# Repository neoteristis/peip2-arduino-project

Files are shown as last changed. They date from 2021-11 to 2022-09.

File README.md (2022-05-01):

# PolyDog V1

## Presentation

> This project has taken place during the Arduino Class of the second year of prep school at Polytech Nice Sophia.  
> In the text, "We" will represent Raphaël Anjou and Hugo Durand, who worked together on this project.  
> We had four months to build any project we wanted as long as it used Arduino hardware. A robot dog was an idea that we found very challenging and entertaining.

> Dozens of other robots inspired us to do this project and helped us in the design of our robot.

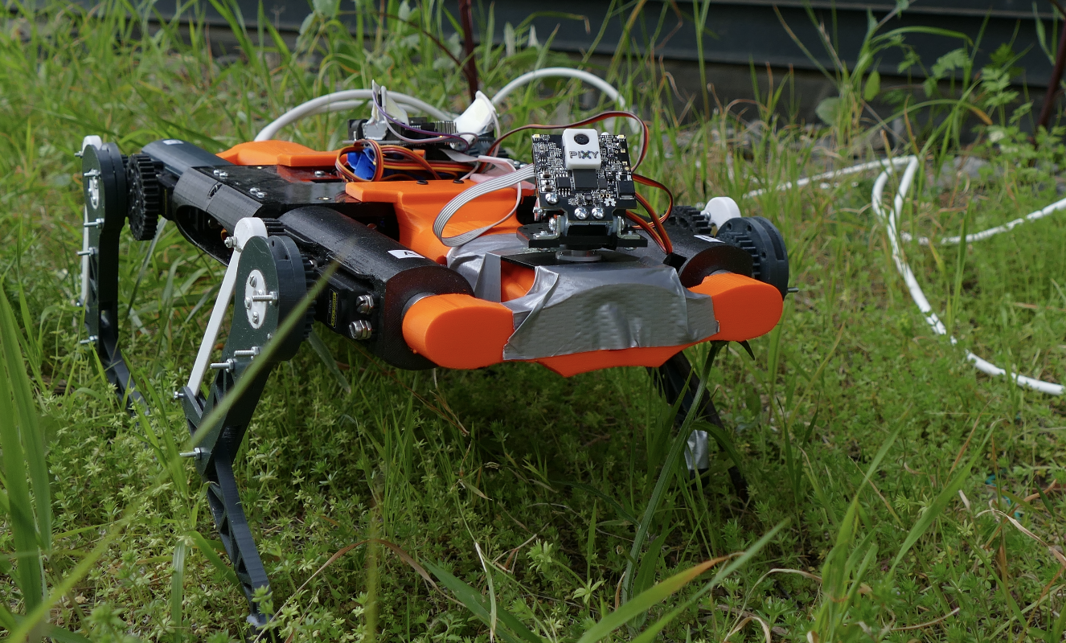
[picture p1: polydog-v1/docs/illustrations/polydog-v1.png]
Robot Pictures


## Summary

- [PolyDog V1](#polydog-v1)
  - [Presentation](#presentation)
  - [Summary](#summary)
  - [Robot Parts](#robot-parts)
    - [Leg parts](#leg-parts)
    - [Body parts](#body-parts)
    - [Electronic Components](#electronic-components)
  - [Flowchart](#flowchart)
    - [Initialization](#initialization)
    - [Remote Control](#remote-control)
    - [Camera](#camera)
    - [Movements](#movements)

## Robot Parts

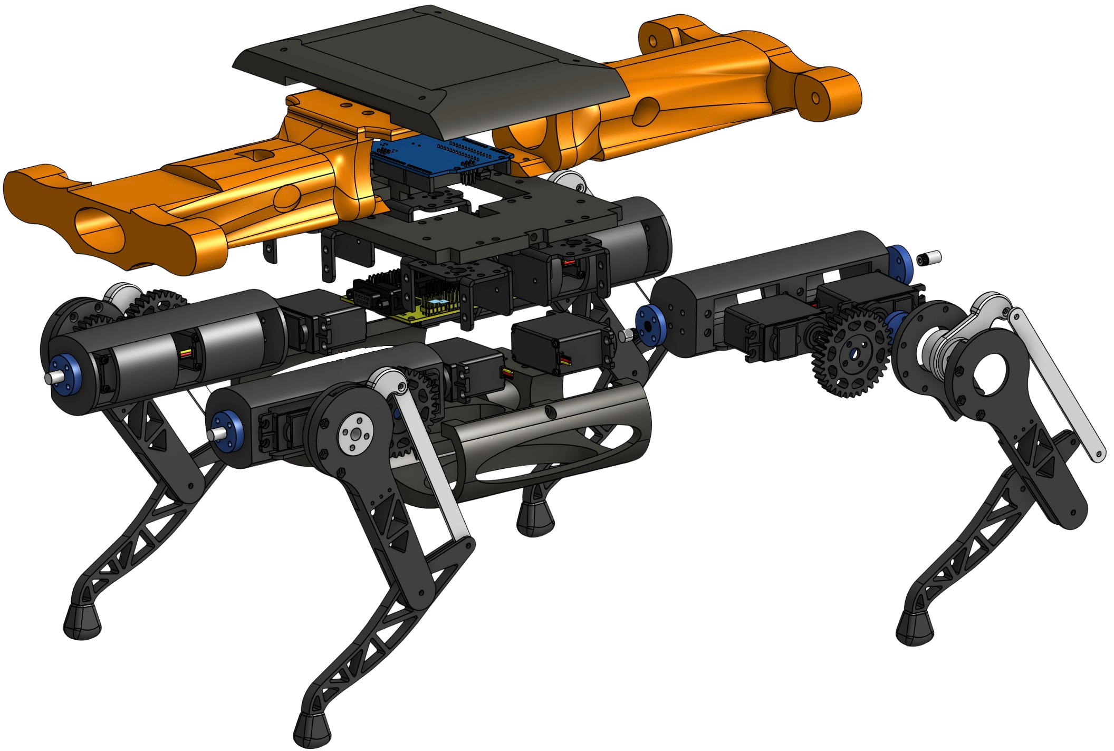
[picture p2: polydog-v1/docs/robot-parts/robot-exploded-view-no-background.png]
PolyDog exploded view


### Leg parts

<table> <!--Table-->
<tbody> <!--Table Body-->
    <tr> <!-- TABLE HEADER -->
        <th align="center" width="80">Name</th>
        <th align="center" width="250">Preview</th>
        <th align="center">Description</th>
        <th align="center" width="75">Material</th>
    </tr>
    <tr> <!--Line-->
        <td align="center">Femur</td>
        <td align="center">
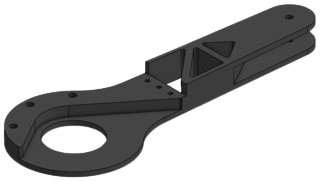
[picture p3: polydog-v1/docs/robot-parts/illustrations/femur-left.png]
            
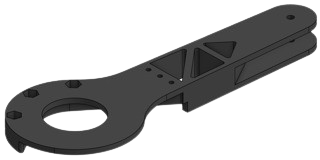
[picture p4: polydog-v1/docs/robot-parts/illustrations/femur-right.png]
            
        </td>
        <td align="center">Attached to the hip to hold the knee. Is connected to the tibia.</td>
        <td align="center">3D-printed</td>
    </tr>
    <tr> <!--Line-->
        <td align="center">Foot</td>
        <td align="center">
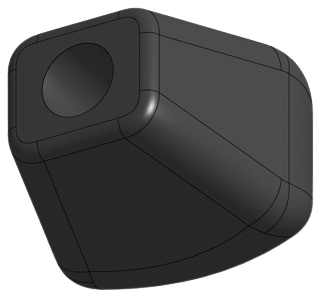
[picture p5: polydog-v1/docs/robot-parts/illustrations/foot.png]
            
        </td>
        <td align="center">Attached at the end of every tibia, it helps with the grip on the floor.</td>
        <td align="center">3D-printed</td>
    </tr>
    <tr> <!--Line-->
        <td align="center">Gear</td>
        <td align="center">
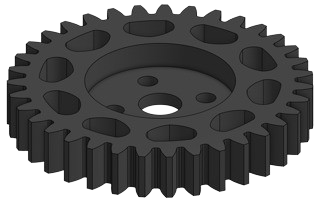
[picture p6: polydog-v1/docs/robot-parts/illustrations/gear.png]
            
        </td>
        <td align="center">Attached to the servo responsible for the whole leg movement. Is connected to the hip.</td>
        <td align="center">3D-printed</td>
    </tr>
    <tr> <!--Line-->
        <td align="center">Hip</td>
        <td align="center">
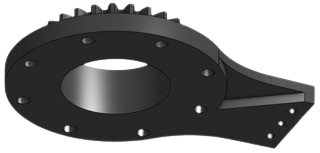
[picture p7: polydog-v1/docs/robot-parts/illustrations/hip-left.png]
            
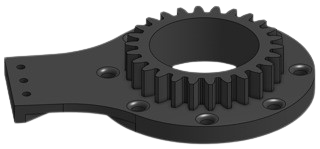
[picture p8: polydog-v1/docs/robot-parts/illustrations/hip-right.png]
            
        </td>
        <td align="center">Link between the servo motor for the whole leg and the femur. Is moved by a gear. Hold the knee in place.</td>
        <td align="center">3D-printed</td>
    </tr>
    <tr> <!--Line-->
        <td align="center">Knee</td>
        <td align="center">
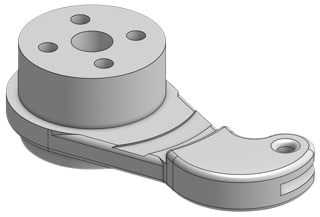
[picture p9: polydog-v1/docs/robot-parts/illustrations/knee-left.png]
            
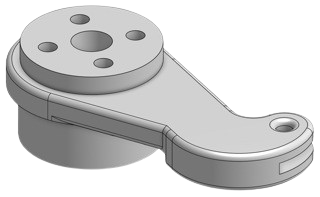
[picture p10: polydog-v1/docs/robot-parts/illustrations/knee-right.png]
            
        </td>
        <td align="center">Link between the servo motor for the knee and the tendon to make the anatomical knee move. Directly attached to the servo.</td>
        <td align="center">3D-printed</td>
    </tr>
        <tr> <!--Line-->
        <td align="center">Leg Holder</td>
        <td align="center">
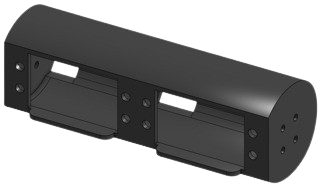
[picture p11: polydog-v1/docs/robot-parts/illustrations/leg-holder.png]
            
        </td>
        <td align="center">Hold the two servo motors necessary to make the leg move.</td>
        <td align="center">3D-printed</td>
    </tr>
    <tr> <!--Line-->
        <td align="center">Tendon</td>
        <td align="center">
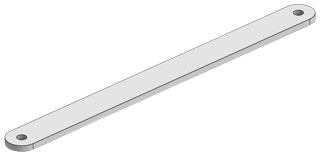
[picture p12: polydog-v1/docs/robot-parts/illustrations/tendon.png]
            
        </td>
        <td align="center">Link between the knee and the tibia.</td>
        <td align="center">3D-printed</td>
    </tr>
    <tr> <!--Line-->
        <td align="center">Tibia</td>
        <td align="center">
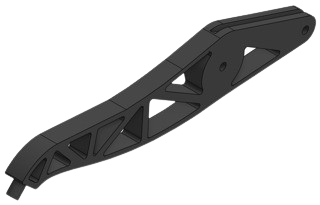
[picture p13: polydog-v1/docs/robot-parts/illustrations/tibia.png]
            
        </td>
        <td align="center">Link between the foot, the femur and the tibia. Is moved by the tendon and rotates around the point where the femur is attached.</td>
        <td align="center">3D-printed</td>
    </tr>
</tbody>
</table>

### Body parts

<table> <!--Table-->
<tbody> <!--Table Body-->
    <tr> <!-- TABLE HEADER -->
        <th align="center" width="95">Name</th>
        <th align="center">Preview</th>
        <th align="center">Description</th>
        <th aling="center" width="75">Material</th>
    </tr>
    <tr> <!--Line-->
        <td align="center">Back</td>
        <td align="center">
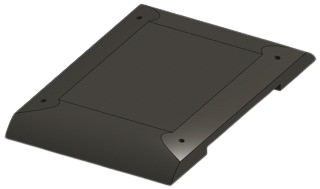
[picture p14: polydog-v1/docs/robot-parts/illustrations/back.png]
            
        </td>
        <td align="center">Close the robot body to protect and hide all the hardware and cables inside.</td>
        <td align="center">3D-printed</td>
    </tr>
    <tr> <!--Line-->
        <td align="center">Base</td>
        <td align="center">
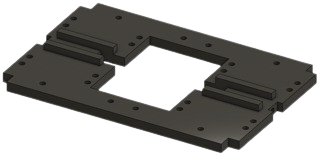
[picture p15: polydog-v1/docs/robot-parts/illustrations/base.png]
            
        </td>
        <td align="center">Core of the body structure.</td>
        <td align="center">3D-printed</td>
    </tr>
    <tr> <!--Line-->
        <td align="center">Ribs</td>
        <td align="center">
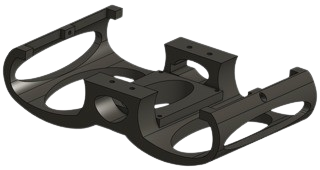
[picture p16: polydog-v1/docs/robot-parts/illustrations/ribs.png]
            
        </td>
        <td align="center">Help with the rigidity of the whole body. Protect the hardware from being hit. Hold the SSC-32.</td>
        <td align="center">3D-printed</td>
    </tr>
    <tr> <!--Line-->
        <td align="center">Servo Bracket</td>
        <td align="center">
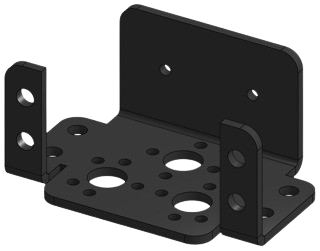
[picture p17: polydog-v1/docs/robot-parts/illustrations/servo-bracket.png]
            
        </td>
        <td align="center">Hold one servo motor in place.</td>
        <td align="center">Aluminium</td>
    </tr>
    <tr> <!--Line-->
        <td align="center">Spine</td>
        <td align="center">
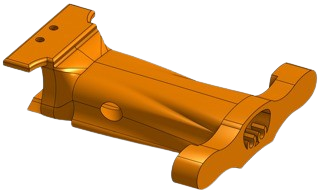
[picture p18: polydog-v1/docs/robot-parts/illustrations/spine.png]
            
        </td>
        <td align="center">Hold two legs and store the power cable.</td>
        <td align="center">3D-printed</td>
    </tr>
</table>
</tbody>

### Electronic Components

<table> <!--Table-->
<tbody> <!--Table Body-->
    <tr> <!-- TABLE HEADER -->
        <th align="center" width="95">Name</th>
        <th align="center">Preview</th>
        <th align="center">Description</th>
    </tr>
    <tr> <!--Line-->
        <td align="center">Arduino UNO</td>
        <td align="center">
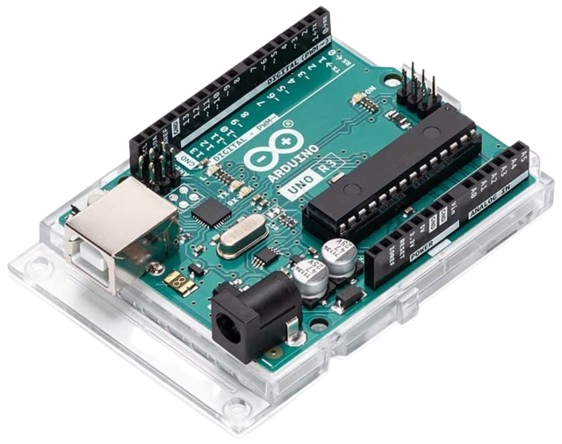
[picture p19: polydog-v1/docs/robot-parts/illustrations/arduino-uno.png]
            
        </td>
        <td align="center">Robot brain.</td>
    </tr>
    <tr> <!--Line-->
        <td align="center">SSC-32 Servo Controller</td>
        <td align="center">
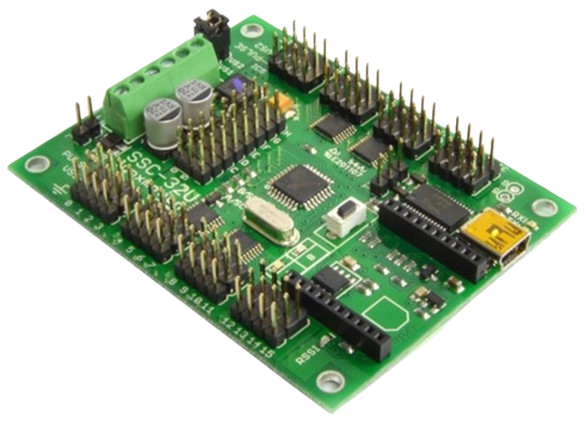
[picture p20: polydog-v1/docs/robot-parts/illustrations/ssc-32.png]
            
        </td>
        <td align="center">Receives command from the Arduino UNO to control every servo motor.</td>
    </tr>
    <tr> <!--Line-->
        <td align="center">Servo motors</td>
        <td align="center">
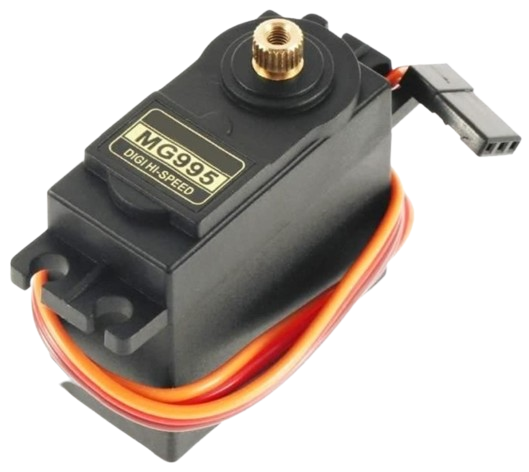
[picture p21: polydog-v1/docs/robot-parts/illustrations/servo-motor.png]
            
        </td>
        <td align="center">Moves the part of the body they are connected to.</td>
    </tr>
    <tr> <!--Line-->
        <td align="center">Infrared Remote & Receiver</td>
        <td align="center">
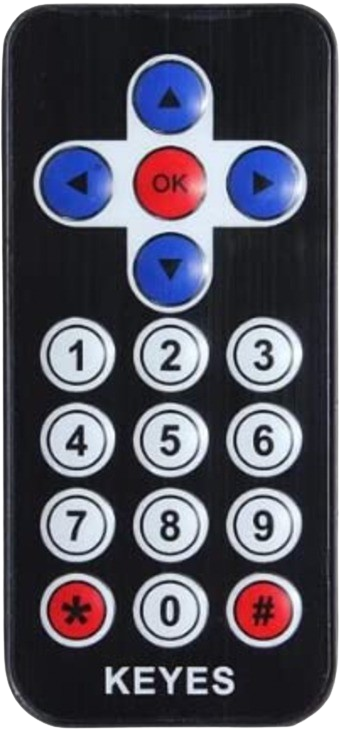
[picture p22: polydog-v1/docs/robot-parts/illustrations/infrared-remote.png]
            
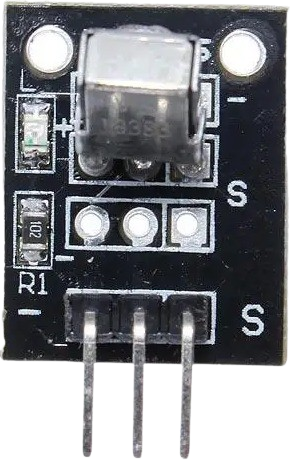
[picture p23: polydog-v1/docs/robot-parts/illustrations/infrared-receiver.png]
            
        </td>
        <td align="center">Remote control of the robot movements and actions.</td>
    </tr>
    <tr> <!--Line-->
        <td align="center">Pixy Cam 2 & Mount</td>
        <td align="center">
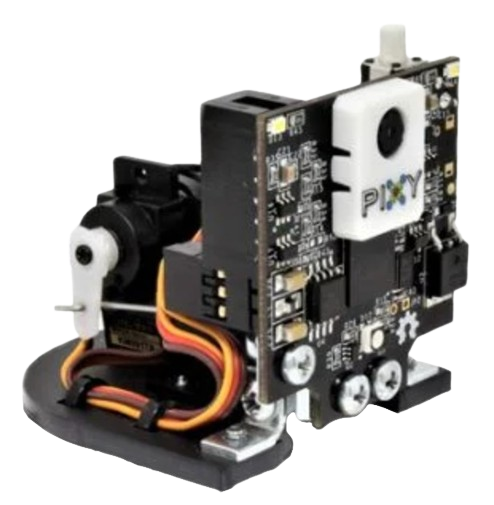
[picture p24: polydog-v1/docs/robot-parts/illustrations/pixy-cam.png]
            
        </td>
        <td align="center">Camera of the robot. Is able to detect colors. The camera can be moved on 2 axis with it's mount.</td>
    </tr>
    <tr> <!--Line-->
        <td align="center">Power source</td>
        <td align="center">
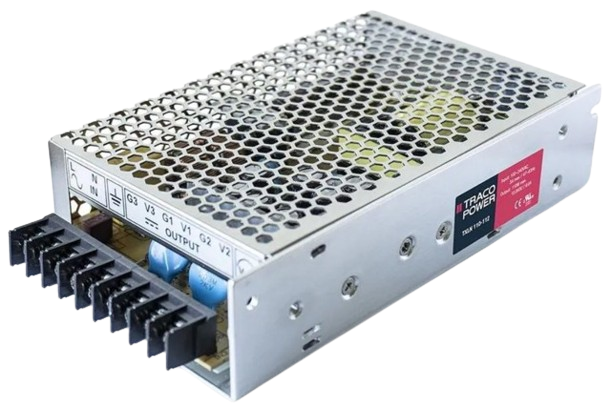
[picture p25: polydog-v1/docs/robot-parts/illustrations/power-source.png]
            
        </td>
        <td align="center">Powers all the electronic components. 30 Amperes and 5 Volts. </td>
    </tr>
</table>
</tbody>

## Flowchart

### Initialization

### Remote Control

### Camera

### Movements

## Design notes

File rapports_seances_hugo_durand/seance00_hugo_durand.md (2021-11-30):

# Première séance : 

début novembre jusqu'au 02/12/2021 

## Emergence de l'idée

Pendant les vacances, je me suis beaucoup documenté sur la plupart des projets Arduino les plus connus. Au début j'étais sûr d'une chose, je voulais créer un robot capable de se déplacer. Raphael était du même avis. 

J'ai alors été intérressé par la cartographie d'une pièce par une voiture, le serpent, l'araignée, la self-balancing robot. En retombant par hasard, sur une vidéo du célébre robot Spot de Boston Dynamics, nous n'avons pas hésité longtemps. On fera un robot chien qui naitra sous le nom de PolyDog.

## Recherche sur les prototypes à notre portée

Au fur et à mesure que l'on cherche, on trouve de plus en plus d'exemples de prototypes. Je me suis d'abord penché sur la patte de notre robot, de comment elle pourrait fonctionner.

Deux manière de faire observée :

- Loki le Dev, un développeur spécialisé en système embarqué et robotique opte pour 3 actionneurs basé sur un système de parallélogramme.

- KiTty bot lui possède un servo moteur directement sur le genou et je trouve ça moins optimisé, du fait que la patte est plus lourde et l'inertie de la patte est augmentée.

On a opté pour la 1ere option. Je l'ai contacté sur Discord pour qu'il m'aiguille sur quelques points et avoir son avis sur notre projet. Il a été très sympa et nous a beaucoup aidés dans le début de nos recherches.

Enfin, on a appris que le défi, une fois le robot construit, sera de le faire tenir debout en équilibre sur ces pattes à l'aide d'un algorithme complexe basé sur le reverse kinematics. On devra entraîner la demarche du robot sur unity, afin qu'il se déplace convenablement.

## Création et impression des pièces

Nous allons créer pour commencer une jambe miniature de notre robot pour manipuler son fonctionnement.

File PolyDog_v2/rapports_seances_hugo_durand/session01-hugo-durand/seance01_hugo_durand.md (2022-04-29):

# Séance 1 - version 2 de PolyDog

## Semaine du 04 avril 2022 - 17 avril 2022

-----

Nous avons eu des difficultés à se mettre en route pour commencer la deuxième version de notre robot chien : PolyDog_v2.

**1. Étape 1 - Bilan et synthèse de la v1 -**

Les points noirs de la version 1 sont :

* Le poids trop élevé du corps. Masse volumique du PETG trop grande.

* Les servo-moteurs ont un couple trop faible (13kg/cm). Le robot a du mal à effectuer des mouvements (cumulé avec un poids trop important)

* L'engrenage entre la hanche et le servo-moteur. L'embout en plastique s'use facilement. Le degré de liberté d'un pas de pignon augmente.

##### Corps en aluminium

Nous avons donc décidé de réaliser le corps du robot en aluminium, assemblé avec des équerres et des charnières.

<figure align="center">
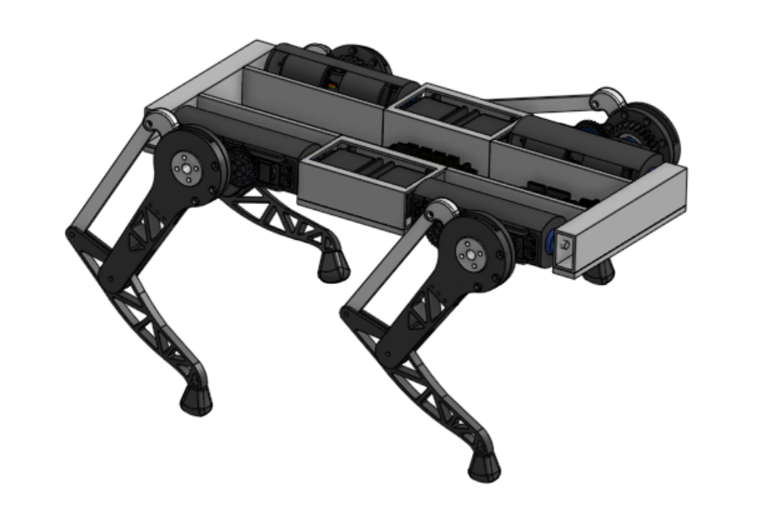
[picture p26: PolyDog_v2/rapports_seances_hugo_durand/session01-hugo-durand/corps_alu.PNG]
  
  <figcaption>Des carrés d'alu viennent se fixer sur une plaque en aluminium ou de plexiglass</figcaption>
</figure>

##### Engrenage double hélice

Pour renforcer la stabilité de l'engrenage, j'ai modélisé deux double helical gear qui vont se coincer dans la roue dentée double helice de la hanche. J'ai trouvé cette idée sur YouTube : https://www.youtube.com/watch?v=pxgut7d135w&t=162s

Cela donne ceci :

<figure align="center">
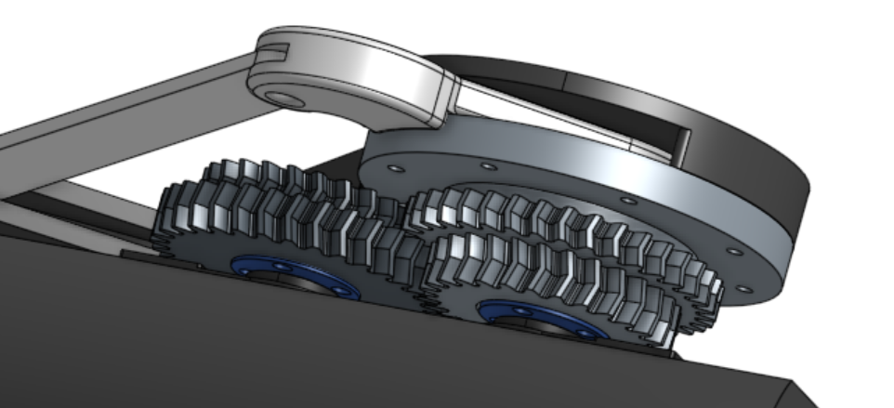
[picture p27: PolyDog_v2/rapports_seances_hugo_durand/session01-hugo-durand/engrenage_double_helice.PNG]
  
  <figcaption></figcaption>
</figure>

>Je n'ai pas encore réussit à modifier l'angle d'offset pour que les deux roues dentées soit synchronisé deux à deux.

En attendant j'ai prédéfini le matériel à acheter pour la construction du corps en aluminium.

**Achat matos:**

* carre d'alu : 32mm (longueur), 16mm (largeur_intérieur), 28 (hauteur_intérieur) ---> prévu 4mm d'épaisseur
<br>
* carre d'alu : 200mm (longeur), 58mm (largeur_intérieur) 28 (hauteur_intérieur) --->prévu 4mm d'épaisseur, je n'y connais rien
<br>
* plaque d'alu ou plaque de pléxiglass: 5mm d'épaisseur, 414 x 184mm;

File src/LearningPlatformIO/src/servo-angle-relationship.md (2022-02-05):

# Servo Angle Relationship

## Context

We are considering the following names for the legs :

> B --- A -> B-A is the front \
> | ....... | \
> | ....... | \
> | ....... | \
> C --- D -> C-D is the rear

Considering X the name of the leg, all motors will be named with the following convention :

- X_hip
- X_knee
- X_shoulder

## Placement of all the motors on the robot

1. A_shoulder
2. A_hip
3. A_knee
4. B_knee
5. B_hip
6. B_shoulder
7. C_shoulder
8. C_hip
9. C_shoulder
10. D_knee
11. D_hip
12. D_shoulder

> 4 --- 3 -> Front \
> 5 ..... 2 \
> 6 ..... 1 \
> 7 ..... 12 \
> 8 ..... 11 \
> 9 --- 10 -> Rear

## Angle relationship

As a baseline, we will use the angles of the A leg. \
Which means that all others should be expressed in function of A_motor_angle.

1. A_shoulder_angle -> baseline
2. A_hip_angle -> baseline
3. A_knee_angle -> baseline
4. B_knee_angle ->
5. B_hip_angle ->
6. B_shoulder_angle -> ?
7. C_shoulder_angle -> ?
8. C_hip_angle -> map(0, 180, 180, 0)
9. C_shoulder_angle -> map(0, 180, 180, 0)
10. D_knee_angle -> baseline
11. D_hip_angle -> baseline
12. D_shoulder_angle -> ?

## TODO

Change A leg motor placement

## TO NOTE BETTER

Pour le genou : 90 degrés
Pour la hanche : 180 degrés

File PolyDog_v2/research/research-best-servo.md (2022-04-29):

| Servo name | Couple | Weight| Rotation speed | Price | Reference |
| :---: | :---: | :---: | :---: | :---: | :---: |
|TowerPro Metal Gear MG995 (**Polydog_v1**)| Couple de décrochage : 13 kg/cm (4,8 V)|55 g | 0,17 sec/60 ° | / | https://www.youtube.com/channel/UCp-MOXWuPocJWpOKq-EK11g |
|Servomoteur HS-85MG Hitec | 3.5 Kg-cm | 21.9g | Vitesse (sec/60o): 0.13 | 33,20 € | https://www.robotshop.com/eu/fr/servo-moteur-hs85mg-hitec.html |
|Servo numérique étanche DS3225MG|maximum torque can reach 21kg.cm (5,0 V)| 67g|(5,0 V): 0,15 sec / 60 degrés|23,99€|https://www.amazon.fr/dp/B08BZNSLQF?tag=takoe-21&linkCode=osi&th=1&psc=1&keywords=Servomoteurs|
|Servo TD-8135MG|35.7 km cm (5,0 V)| 85g|(5,0 V): Noload speed:0.32sec/60°-0.22sec/60° / 60 degrés|$17.99 |https://www.ebay.com/itm/283885400511|
|Coreless digital servo TD-8135MG (**Polydog_v2**)|Couple de décrochage de pointe: 32.7kg.cm - 35.2kg.cm| 56g|Vitesse à vide: 0.32sec/60 ° - 0.22sec/60 °|13,90 euros |https://fr.aliexpress.com/item/4000538643378.html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|

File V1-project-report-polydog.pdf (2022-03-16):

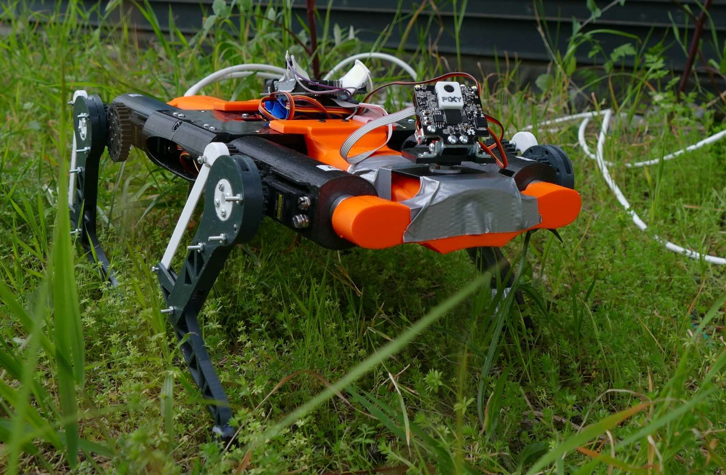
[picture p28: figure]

– Polytech Nice-Sophia – | 2021-2022
ANJOU Raphaël | Peip2 – Arduino
DURAND Hugo | M. Pascal MASSON

# RAPPORT DE PROJET ROBOT POLYDOG

Fig. 1 : Le PolyDog dans son habitat naturel

2

## SOMMAIRE

Planification / Réalisation

Hardware

Software

3

## Introduction

Dans le cadre du cours d’Électronique-Arduino de la 2ème année du cycle préparatoire à l’école de Polytech Nice Sophia, nous avons eu l’occasion de créer de A à Z un projet de notre choix. Le temps imparti pour cette réalisation était de 8 séances de TD étalées sur un peu plus de 3 mois. Cependant, nous avons commencé à réfléchir à ce que l’on avait le plus envie de construire un mois avant le début des cours.

Le but de ce projet était de nous donner le goût d’innover grâce à des technologies que nous n’utilisions pas telles que la découpe laser, l’impression 3D ou le fer à souder. Il avait pour vocation de nous former au travail en équipe, ainsi que nous permettre de mettre un pied dans le métier d’ingénieur. Pour ce faire, le projet a débuté par la présentation d’un cahier des charges, d’un diagramme de Gantt. Le suivi du projet a ensuite eu lieu grâce à la rédaction de rapports de séance incluant tout le travail fournit entre deux séances.

En effectuant nos recherches sur Internet, principalement YouTube, nous avons pu trouver de nombreux exemples de ce qui était faisable grâce à l’Arduino. Nous étions sûr de deux choses, nous voulions que ce soit un robot qui puisse se déplacer et que ce soit une première dans l’école. Nous avons hésité entre un bras robotisé automatisé ou un robot issu du biomimétisme.

C’est à ce moment que jaillit l’idée d’un robot chien que nous avons baptisé POLYDOG. Nous l’avons conçu dans le but de déplacer un corps à 4 pattes dans les 4 directions basique : gauche, droite, avant, arrière. Il est doté d’une PixyCam et d’un module Infrarouge pour une communication à distance des mouvements.

Ainsi, la problématique de notre sujet est : Par quels moyens déplacer un robot sur 4 pattes ?

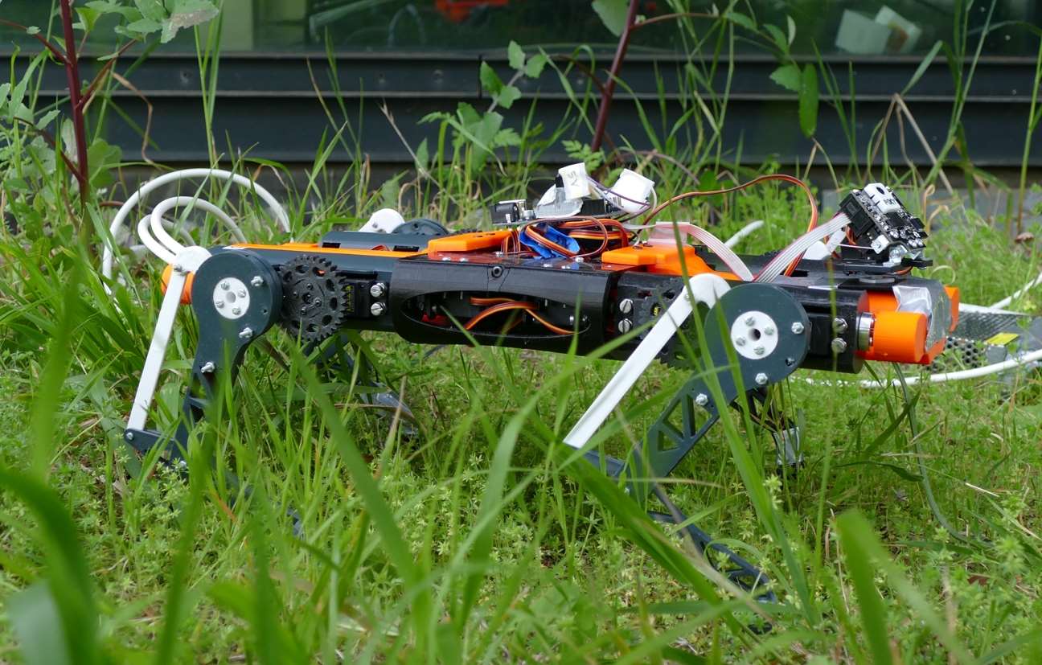
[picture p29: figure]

Fig. 2 : Le PolyDog se cache dans les fourrés

4

## Cahier des charges

### Reprenons notre cahier des charges initial et faisons un point sur les objectifs que nous nous étions fixés :

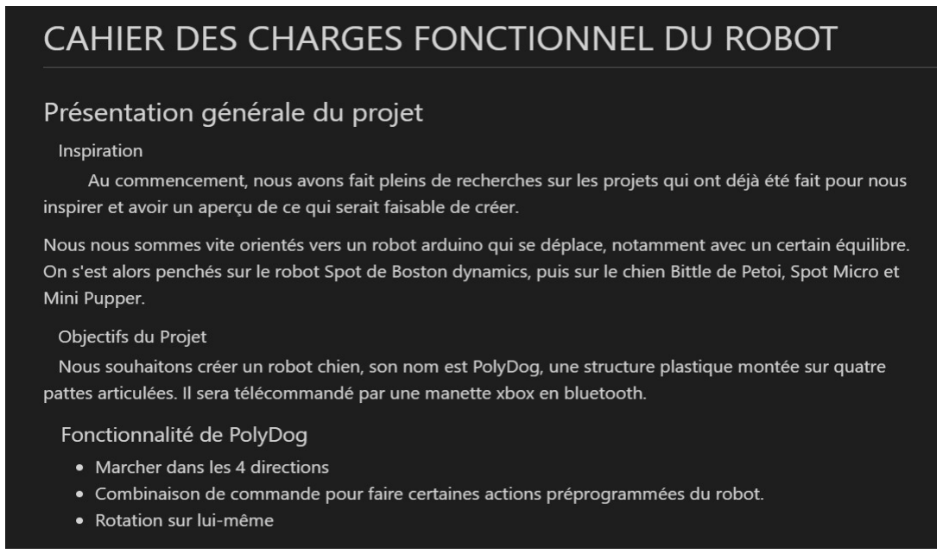
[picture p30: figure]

### 2.1/ Fonctionnalités réalisées

Nous avons quasiment rempli l’objectif principal : notre robot peut marcher en avant et sur les côtés, avec des combinaisons de commande pour faire certaines actions préprogrammées du robot.

Cependant, nous avions pour objectif qu’il soit télécommandé par une manette de Xbox. Nous ne sommes pas arrivés à ce degré de complexité, en revanche, nous avons équipé le robot de commandes à distance infrarouges.

De plus, nous n’avons pas eu la possibilité de réaliser la fonctionnalité lui permettant de tourner sur lui-même.

### 2.2/ Fonctionnalités optionnelles

Nous avons équipé Polydog, d’une caméra intelligente qui suit un objet d’une certaine couleur. Le module PixyCam installée sur son socle à l’avant du robot. Lorsqu’elle détecte un objet bleu, le robot avance tout droit.

5

### 2.3/ Diagramme de Gantt et Planning réel

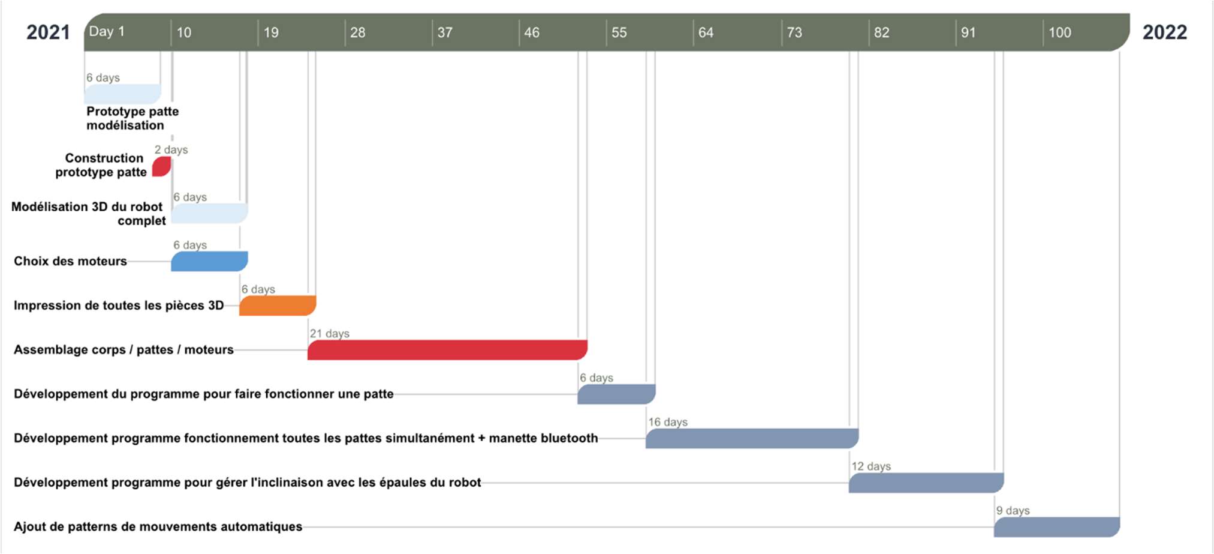
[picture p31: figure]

Fig. 3 : Diagramme de Gantt initial

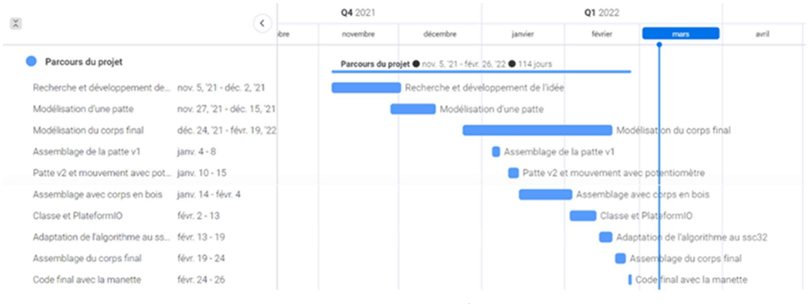
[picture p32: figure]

Fig. 4 : Planning réel

La modélisation 3D du robot complet a pris beaucoup plus de temps que prévu. Cela vient du fait de l’évolution de notre vision du robot et de ses composants. Il faut savoir que nous avons eu beaucoup de problème au niveau de la puissance des moteurs et de l’équilibre du robot. Pensant que le problème venait de la gestion des circuits de la carte, nous avons changé 4 fois de système électronique :

- Driver Adafruit + ArduinoNano
- ArduinoMega2560+ Base Shield + SensorShield (Empilés les uns sur les autres pour obtenir les pins adéquat)
- MegaStrong + Board micro controller intégré
- ssc32- servo controller + Arduino UNO

A chaque changement de système, nous avions l’impression de revenir en arrière du fait de devoir changer le programme et aussi l’organisation des pattes pour des raisons parfois inconnues.

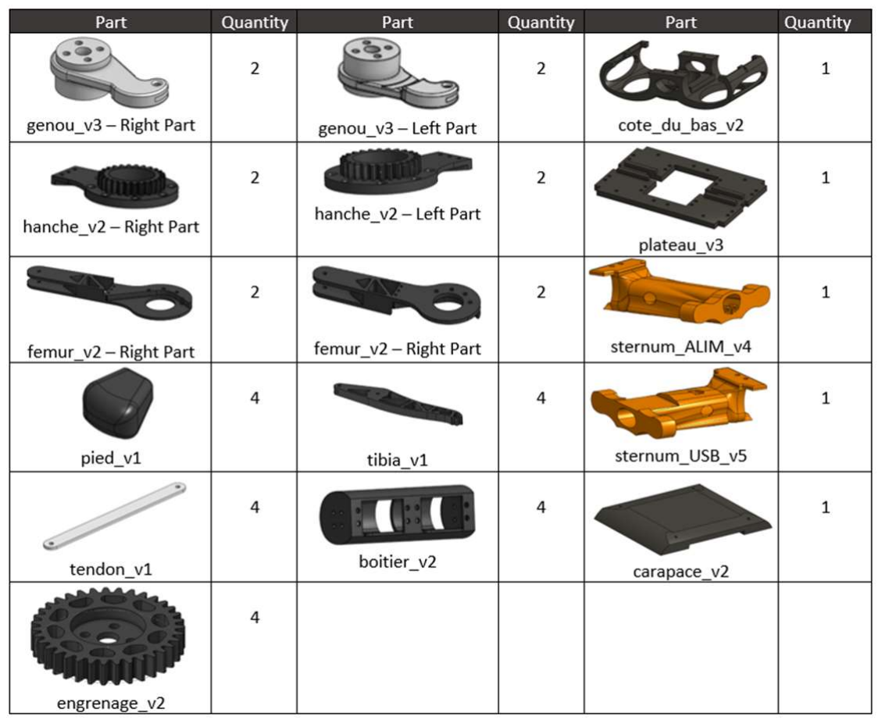
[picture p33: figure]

6

# Hardware

### 3.3/ Pièce 3D

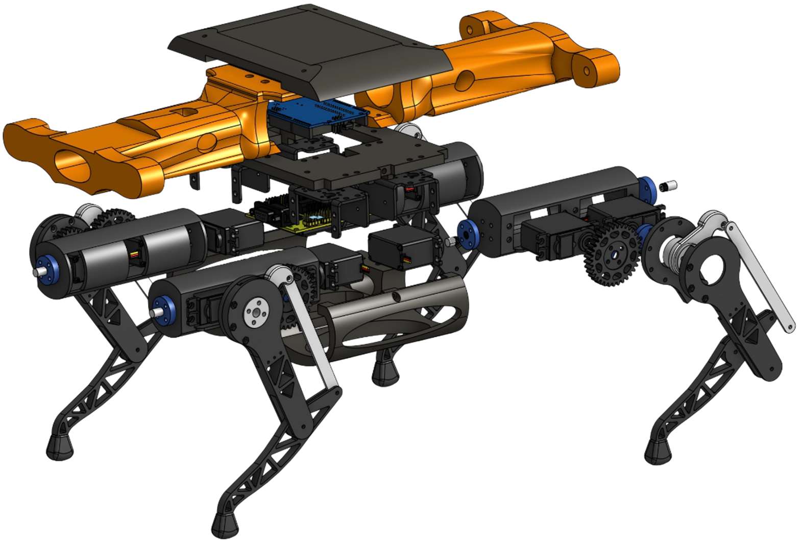
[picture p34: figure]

La conception a été réalisé sur OnShape, un logiciel en ligne, gratuit pour les étudiants.
Le boîtier pour les moteurs a été choisi circulaire pour pivoter avec plus de liberté de gauche à droite.

Nous avons rencontré des difficultés dans la conception de certaines pièces. Les côtes du bas devait s’emboiter avec le plateau avec les moteurs déjà fixés dessus. Nous avons dû faire face également au problème du poids. Les deux pièces sternum et les côtes du bas ont été optimisées pour peser le moins possible tout en gardant une certaine solidité.

Durant l’assemblage, 2 pièces ont été endommagées. Avec un peu de colle, l’emboîtement a pu se faire sans trop de
problèmes.

Cependant, le montage du robot entier en abandonnant le
corps en bois l’a rendu trop lourd ce qui a réduit ses capacités de mouvement.

Le poids cumulé de toutes les pièces pèse sur l’équilibre et la mobilité des pattes.

Cependant, nous ne regrettons pas, car nous y avons appris beaucoup de choses : conserver une marge entre les pièces car l’impression a une imprécision de 0,4 mm ; mettre des inserts dans le plastique ; choisir minutieusement l’emplacement des vis.

Si c’était à refaire, j’opterais pour un corps encore plus léger, en dépits que les fils pendraient sur le côté et au-dessus du robot. Le rendu final serait moins ordonné mais plus mobile.

Composition du robot :

Il mesure 17,6 cm de large sur 42,4 cm de long. Il pèse environ 2 kilogrammes.

### 37 pièces 3D indépendantes

assemblées avec 142 vis,
plus de 142 écrous et 14
inserts.

Le temps d’impression peut s’estimer à plus de 100
heures.

7

### 3.2/ Fonctionnement de la patte

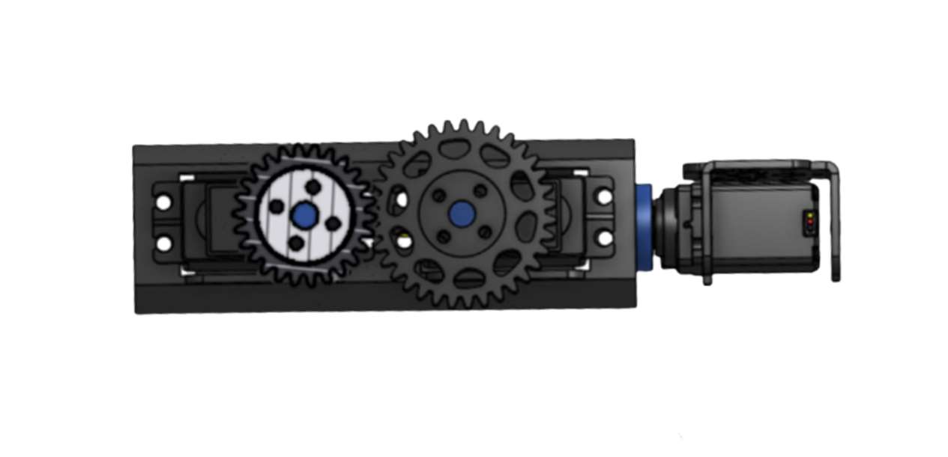
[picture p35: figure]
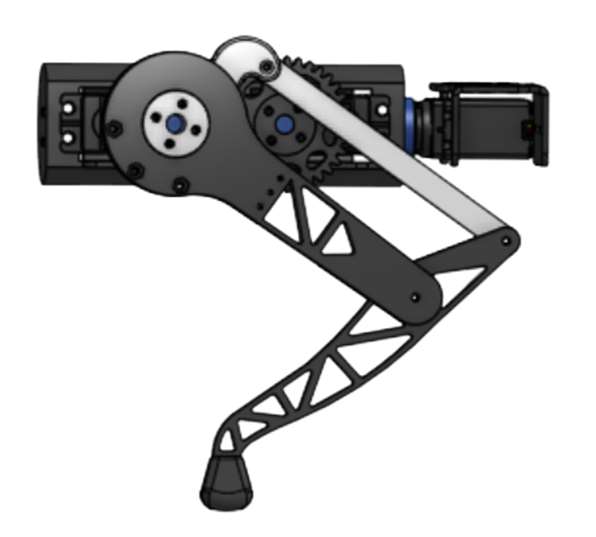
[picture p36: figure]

Nous avons opté pour un fonctionnement d’une patte avec le modèle du parallélogramme. Les moteurs sont centralisés au niveau du corps du robot pour garder la patte légère et une optimisation du mouvement.

Une patte du robot est munie de 3 servos moteurs. Le 1er servo en partant de la gauche est celui qui bouge le genou (au centre de la patte). Le genou est positionné de tel sorte que l’amplitude de mouvement (0° à 180°) du servo associé correspondent aux angles désirés.
Le 2e
est relié à un engrenage de 35 dents vers 26 dents qui bouge la hanche. De ce fait le rapport entre les deux engrenages augmente l’amplitude de mouvement de la hanche de 1,35, pour obtenir 0° minimal jusqu’à 242° maximal.
Le 3e
est fixé au corps principal du robot et permet de faire pivoter la patte sur le côté. Pour soutenir le boitier, on place une fixation pivot à l’autre extrémité.

Le pied du robot est fait en plastique élastique caoutchouteux. Cela permet d’obtenir une plus grande adhérence au sol.

### 3.3/ Composants électroniques

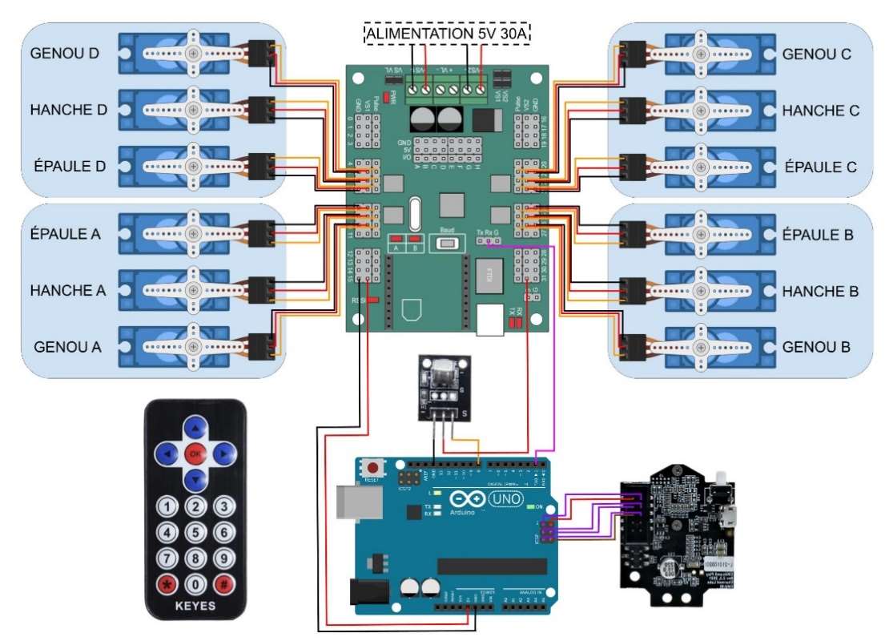
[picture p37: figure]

Nous avons ici, l’ensemble des composants électroniques utilisés pour notre projet. Nous avons 12 servo moteurs branchés sur un ssc32-servo controller qui communique par l’intermédiaire du Serial avec une Arduino UNO. Cette dernière est le composant central puisqu’elle relie sur ses ports, la PixyCam et le récepteur infrarouge. L’ensemble est alimenté sur secteur par l’intermédiaire d’une alimentation de 5V et 30A.

8

# Software

### 4.1/ Classes du programme

La partie code de notre projet a été implantée sur un espace de travail PlateformIO. Il permet de créer un code source unique pour de multiples environnements facilement (Arduino Uno, Mega 2560, etc). Dans le dossier source, nous avons 3 classes :

- CustomServos :

Cette classe permet de communiquer avec le SSC32 en indiquant seulement un angle. On instancie un objet de cette classe à partir d’un numéro de pin.

void CustomServo::move(int position, int time) | Par l’intermédiaire de la carte Arduino, on envoie des
{ | commandes sur le Serial du ssc-32. Le message
Serial.print("#"); | envoyé est de la forme « #{numéro_pin} P {position
Serial.print(_pin); | entre 500 et 2500} T {time}
Serial.print(" P");
Serial.print(position); | Nous n’utilisons pas le paramètre temps dans la
Serial.print(" T"); | fonction move. Cela nous permet d’avoir la liberté de
Serial.println(time); | faire varier le temps dans les méthodes codant les
} | mouvements du robot.
void CustomServo::write(int angle) | La fonction write renvoie la fonction move en
{ | convertissant l’amplitude 500-2500° en 0-180°. Cela
move(map(angle, 0, 180, 500, 2500), 0); | facilite la compréhension physique des mouvements
}
- Leg :

Permet de contrôler chaque moteur d’une jambe sans se soucier des décalages. Par exemple, les moteurs de la hanche n’ont pas les mêmes orientations entre la gauche et la droite. Pour permettre une synchronisation des moteurs des 4 pattes, nous avons pour certains, ajouter un offset de 170°.

- PolyDog :

Cette classe est en quelque sorte un répertoire des méthodes qui vont permettre de donner vie à notre chien. On y définit la méthode self_balancing(), hold_shoulder(), move_forward(), move_right(), move_left(), etc

Les angles de chacun des servos moteurs sont choisis à partir de nombreux test d’optimisation du mouvement de la patte.

void PolyDog::hold_shoulders() | Voici un exemple simple d’une méthode dans la classe Polydog.
{ | Cette méthode maintient les pattes perpendiculaires au sol.
legA.move_shoulder(90);
legB.move_shoulder(90); | On remarque que cette méthode utilise la classe Leg pour gérer les
legC.move_shoulder(90); | décalages dû à notre installation des servo moteurs.
legD.move_shoulder(90);

du robot.

9

### 4.2/ Algorigramme

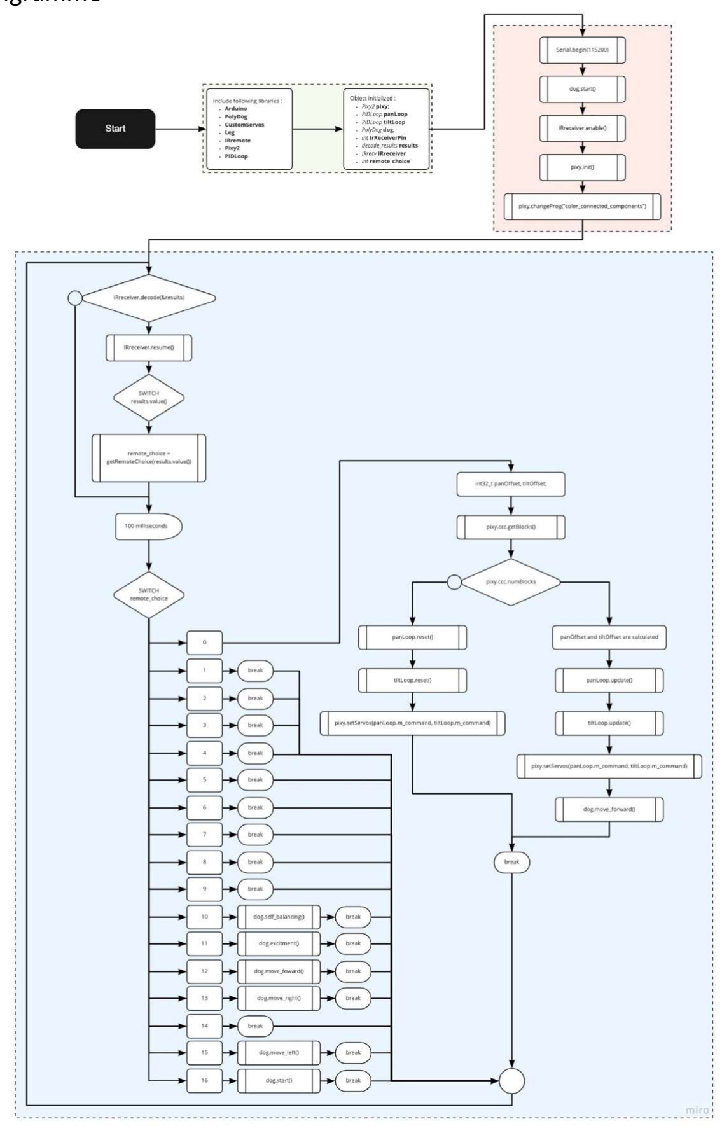
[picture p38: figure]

Les librairies et modules sont d’abord importés (partie verte). Ensuite, les objets utilisés sont instanciés au début du programme (partie rouge). C’est à ce moment-là que le robot est allumé ainsi que la PixyCam et la communication infrarouge. Le robot est alors debout. Enfin, une boucle détectant l’appui des boutons de la télécommande permet de choisir les actions du robot. Par exemple, si l’on appuie sur le bouton 0, le robot utilise la PixyCam pour détecter s’il y a un objet bleu. Si c’est le cas, il se dirige vers l’avant, sinon il se maintient debout. Les autres boutons lui permettent d’effectuer un enchainement de mouvement en boucle ou de se déplacer.

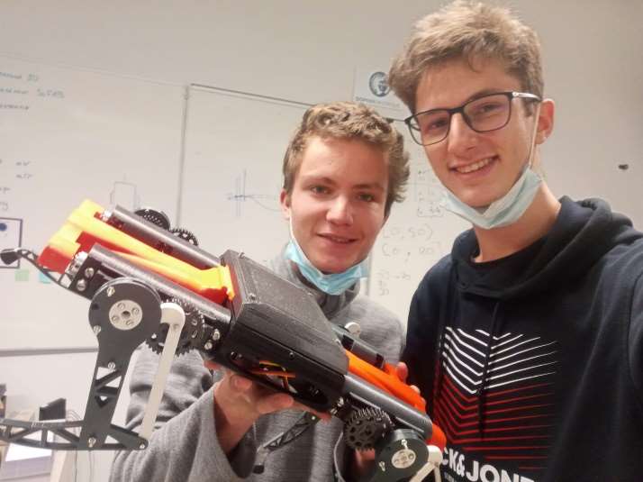
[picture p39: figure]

10

# Conclusion

Ce projet Arduino était motivant et nous a apporté beaucoup de nouvelles compétences. Nous avons appris que le temps de réalisation d’une tâche est très variable. Nous nous sommes formés sur l’utilisation de nouveau outils et de nouveaux logiciels. Notre perception du projet a évolué au fur et à mesure de notre gain d’expérience.

C’est une belle aventure qui nous a fait découvrir le monde de la robotique. Cela a conforté Hugo dans son choix d’aller en robotique l’année prochaine et a conforté Raphaël dans son choix d’aller en SI.

# Perspective

Certes, notre robot chien Polydog marche et est télécommandé. Nous avons pu placer une caméra intelligente qui n’était pas prévu au départ. Nous avons appris de beaucoup de nos erreurs et surmonter des difficultés telles que la non-réponse des servo-moteurs, des angles incohérents, des problèmes de communication entre cartes Arduino, etc…

Cependant, le résultat n’est pas réellement convaincant. Il avance et se déplace en général d’une distance très faible (1cm par seconde en moyenne). Pour certains mouvements, il faut le soutenir un petit peu pour l’alléger artificiellement.

C’est pourquoi, nous considérons ce robot, comme la version 1, le premier jet. Nous prévoyons de commencer une nouvelle version avec un corps en aluminium ou impression résine et de meilleurs servo moteurs, et surtout l’expérience acquise au cours de 3 mois de travail. Nous avons une dizaine de semaine pour le finir et nous sommes plus motivés que jamais pour y arriver.

## Bibliographie

Inspiration :

https://www.youtube.com/watch?v=3_MtMmjEwa4&t=180s

https://www.yeggi.com/q/boston+dynamics/

https://grabcad.com/library/walking-quadruped-robot-diy-1

Lien guide Lynxmotion ssc32-servo controller :

http://www.lynxmotion.com/images/data/lynxmotion_ssc-32u_usb_user_guide.pdf

Guide de mise en marche de la télécommande IR :

https://www.gotronic.fr/pj2-36228-2302.pdf

https://www.gotronic.fr/pj2-codes-gt017-2234.pdf

Notre chaîne YouTube :

https://www.youtube.com/channel/UCp-MOXWuPocJWpOKq-EK11g/featured

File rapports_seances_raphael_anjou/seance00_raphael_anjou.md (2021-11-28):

# Séance 0 : 23/11/2021 --> 01/12/2021

&nbsp;&nbsp;&nbsp;&nbsp;Le travail compris dans la séance 0 correspond au travail préliminaire effectué avec la première
séance en classe avec les enseignants.

### Étape 1 : Choix du projet

&nbsp;&nbsp;&nbsp;&nbsp;Hugo et moi-même souhaitions réaliser un robot capable de se déplacer et pouvant être téléguidé.
Très impressionné par le robot chien **Spot** de ***Boston Dynamics***, nous avons tout d'abord recherché si d'autres 
personnes avaient eu la même idée que nous et avaient réalisé des versions réduites de ce robot. 
Bien évidemment, des dizaines de projets similaires existent sur Internet. Cela nous a rassuré dans notre idée et nous a
motivé à avancer. C'était décidé, nous allions faire un robot chien !

### Étape 2 : Création et mise en place du github

&nbsp;&nbsp;&nbsp;&nbsp;Avant d'aller plus loin dans nos recherches, nous avons décidé de mettre en place au plus vite 
un repository github fonctionnel afin de pouvoir se partager facilement nos recherches. Nous utilisons aussi un groupe
discord dédié au projet Arduino.

La structure actuelle est la suivante : 

```
.
+-- docs
|   +-- cahier_des_charges.md
|   +-- liste_du_materiel.md
|   +-- masson_presentation_deroulement_projet.pdf
|   +-- masson_propositions_projets.pdf
|   +-- masson_tuto_github.pdf
+-- miniature_robot_parts
+-- rapports_seances_hugo_durand
+-- rapports_seances_raphael_anjou
+-- research
+-- robot_parts
+-- src
+-- test
+-- .gitattributes
+-- .gitignore
+-- CMakeLists.txt
+-- README.md
```

### Étape 3 : Création d'une milestone dans github ainsi que plusieurs issues
&nbsp;&nbsp;&nbsp;&nbsp;Nous avons créé une milestone dans github intitulée `Documents, research and setup of the project`.
Dans cette milestone, 10 issues ont été créées afin de lister les tâches nécessaires à faire avant même la première séance
de cours.

### Étape 4 : Recherches générales sur le projet

&nbsp;&nbsp;&nbsp;&nbsp;Cette étape nous a permis de se faire une idée globale des difficultés et challenges techniques
que nous allions rencontrer. Nous avons ainsi étudié le design de nombreux robots disponibles en ligne que ce soit au
niveau du fonctionnement, du design ou des matériaux utilisés.

&nbsp;&nbsp;&nbsp;&nbsp;Parmi nos investigations, Hugo a trouvé la chaîne Youtube de ***Loki Le Dev***. Celui-ci est en
train de réaliser un projet similaire au nôtre, mais dans des envergures bien plus grandes. Hugo l'a contacté et Loki a
été très cordial durant nos échanges et nous a même donné accès aux fichiers 3D d'une jambe de son robot.

&nbsp;&nbsp;&nbsp;&nbsp;Nous avons aussi fait des recherches techniques notamment sur les différents mécanismes permettant
de faire bouger une jambe. Il semble judicieux d'après ce que nous avons trouvé d'utiliser la technologie du "parallélogramme"
qui permet de garder les moteurs au niveau du corps du robot. Contrairement à d'autres méthodes qui nécessitent d'avoir
un moteur au niveau du genou, mais cela nous paraissait trop complexe.

&nbsp;&nbsp;&nbsp;&nbsp;Les recherches sur les algorithmes ont aussi commencés. Ainsi, nous allons probablement travailler
sur un programme capable de faire du "inverse dynamics" car celui-ci est plus simple et efficace que le "forward dynamics".
Nous avons aussi trouvé des exemples de simulations de robot permettant d'entraîner virtuellement notre robot à se déplacer
sur différents terrains.

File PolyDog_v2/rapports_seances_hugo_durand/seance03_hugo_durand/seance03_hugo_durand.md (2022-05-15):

# Séance 3 - version 2 de PolyDog

## Semaine du 09 mai

-----

Le processus d'impression est toujours un peu long. Il nous a fallu 1jours et 7heures pour imprimer les boîtiers. 21 heures pour une patte du robot. 

Nous avons été forcé de lancer deux fois les impressions de la patte parce que la première fois nous avons oublié de mettre des supports.

Enlever des supports nous prends à chaque fois beaucoup de temps. Deux des boîtiers de moteurs se sont fêlés en enlevant le support à l'interieur. Raphael a remis du plastique sur la fissure pour consolider le tout pour le moment. Si cela pète, on reimprimera de nouveau, en remodelisant le boîtier pour qu'il soit un peu plus solide.

En mettant les boîtiers dans leur emplacement, je me suis rendu compte que la longueur que j'avais calculer pour que cela rentre était erronée. Nous avons donc dû reculer l'emplacement des servos et scier une partie de la tranche du carré d'alu.

Concernant les engrenages, j'avais dans les séances précédentes créer un système d'engrenage avec deux pignons à chevrons superposés en contact avec deux autres pigons de cette façon : 

<figure align="center">
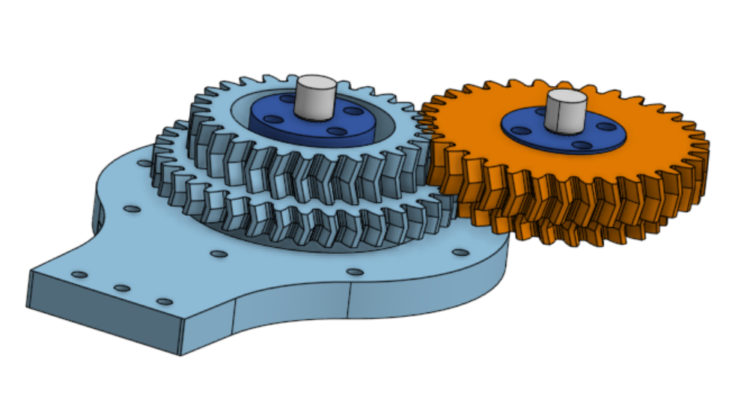
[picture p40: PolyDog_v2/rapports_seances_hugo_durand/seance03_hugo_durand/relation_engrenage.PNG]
  
  <figcaption></figcaption>
</figure>

Une fois imprimé, nous nous sommes rendu compte que les deux engrenages ne sont pas synchro, il y a un petit bloquage. Cependant indépendamment l'un de l'autre, les relations sont correcte. 

Ceci est peut être dû à Onshape qui ne conservent pas le clocking angle que je lui octroie. Donc la solution serait de le refaire sur Fusion360. Deuxième solution est de faire les pigons avec le même rapport de taille, et que les dents du petit pignons soit alignés avec celle du grand.

Si ceci ne fonctionne pas alors je garderai juste un des pignons de chaque.

Les maintiens de roulement ont tous été imprimés : 

<figure align="center">
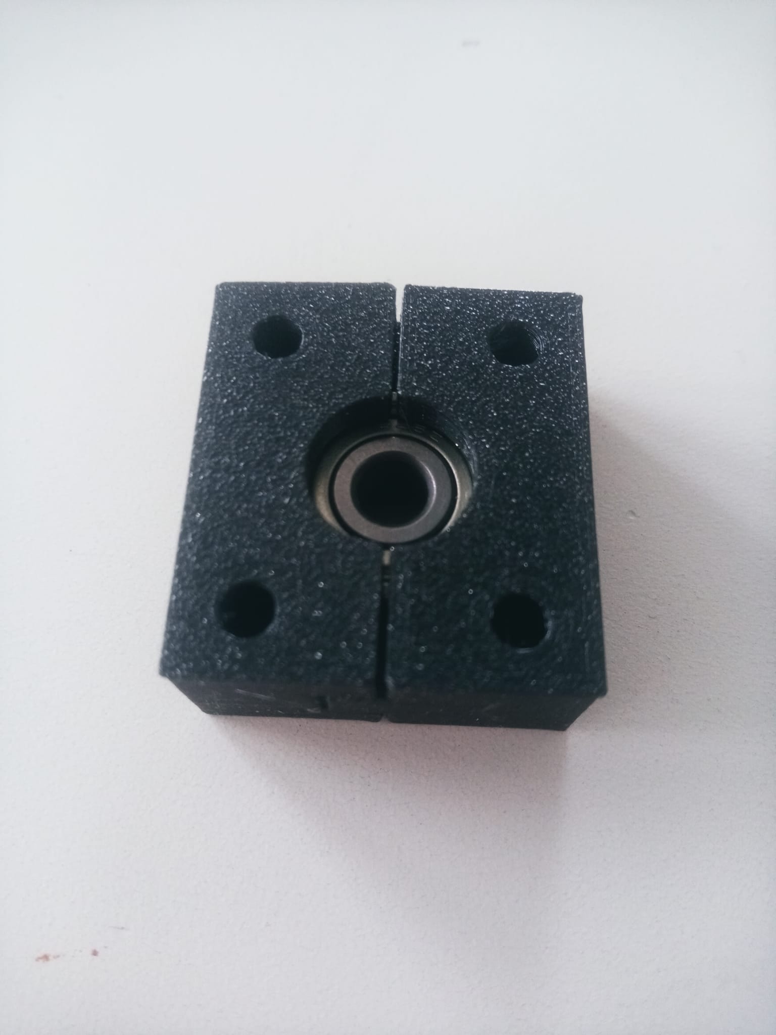
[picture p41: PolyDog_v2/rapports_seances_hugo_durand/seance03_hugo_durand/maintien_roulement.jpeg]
  
  <figcaption></figcaption>
</figure>

J'ai scié la tige en métal, fixer les embouts qui maintiennent le boîtier de la patte dans son axe.

J'ai compris ce qui n'allait pas dans les engrenages. Lorsque je faisais une vue ne coupe pour vérifier la relation entre les engrenages, je la faisais au milieu d'une tranche hélicoïdal. Je referais une nouvelle impression pour tester.

J'ai également renforcer les boîtiers de servo moteurs pour si jamais on les reimprime.

<figure align="center">
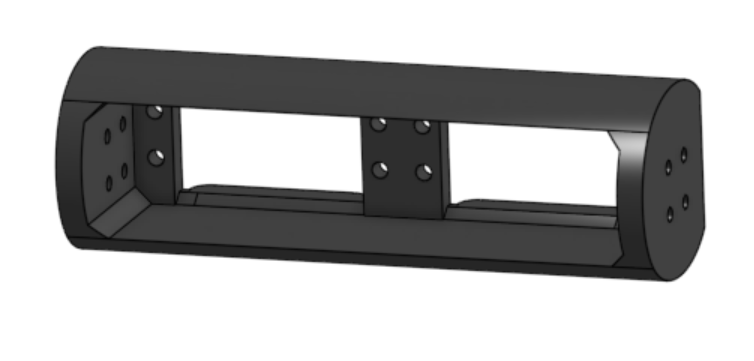
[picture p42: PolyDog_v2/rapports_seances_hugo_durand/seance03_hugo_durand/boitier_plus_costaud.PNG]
  
  <figcaption></figcaption>
</figure>

Pour finir j'ai crée les support de la carte ARDUINO UNO et le servo controller SSC32 :

<figure align="center">
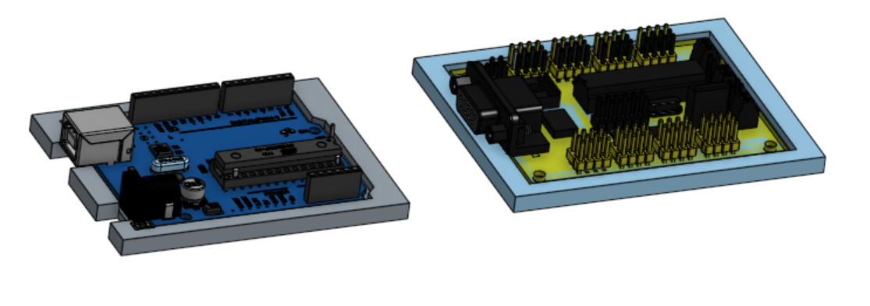
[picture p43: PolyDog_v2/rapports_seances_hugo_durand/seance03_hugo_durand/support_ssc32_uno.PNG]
  
  <figcaption></figcaption>
</figure>

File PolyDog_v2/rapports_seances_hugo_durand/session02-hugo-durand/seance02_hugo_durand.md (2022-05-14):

# Séance 2 - version 2 de PolyDog

## Semaine du 25 avril

-----

A castorama ou a leroy merlin, il n'y pas un éventail de taille et dimension extraordinaire. Nous avons donc constitué nos propres carrés d'alu.

On a chipé deux-trois plaques d'alu de différentes épaisseurs qu'on pouvait trouver.

On a commencer par la plaque d'alu, support principale du corps:

<figure align="center">
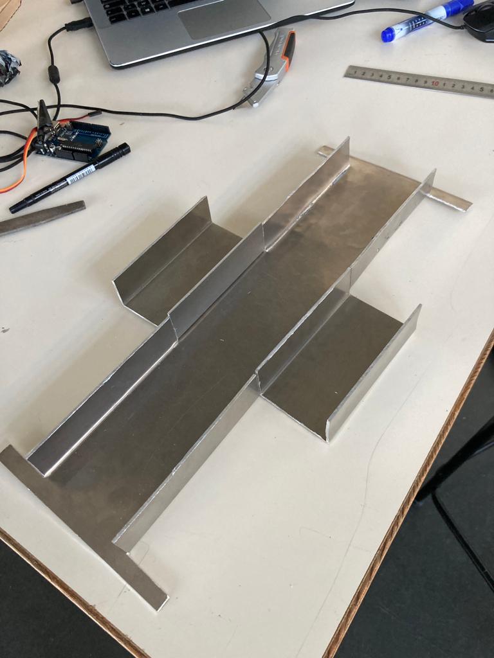
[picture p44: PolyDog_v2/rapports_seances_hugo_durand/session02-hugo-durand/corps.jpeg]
  
  <figcaption></figcaption>
</figure>

Nous avons eu un peu de mal, pour plier les bouts de métal. La plieuse apporte des contraintes au niveau des pliages à la suite du premier pliage, car la plaque ne passe plus dans la machine. On a fini le travail à coup de marteau, laissant des finitions pas tip top.

<figure align="center">
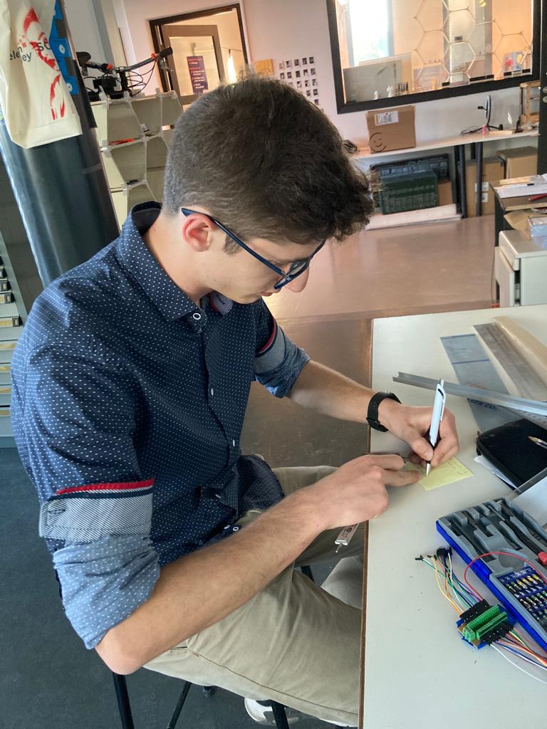
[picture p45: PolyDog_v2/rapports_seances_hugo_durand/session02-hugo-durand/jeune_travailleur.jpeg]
  
  <figcaption></figcaption>
</figure>

On a fait de nombreuses mesures sur la taille des découpes de l'alu pour que les pièces s'emboitent et se rivete ensemble correctement. 

//Photo des carrés d'alu avec le moteur. //

L'outils par excellence pour notre découpe a été la dremel. Bien que par endroit, c'est plus rapide de la faire à la scie.

<figure align="center">
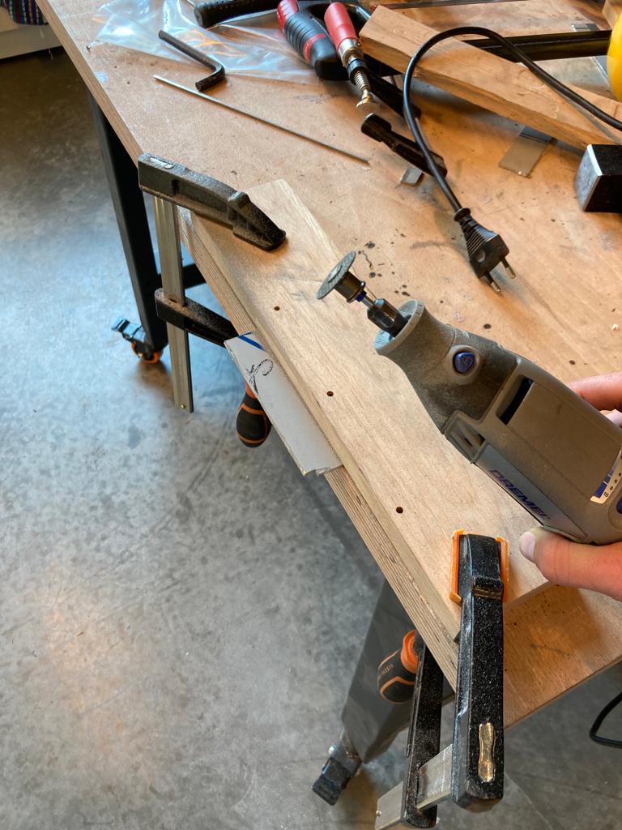
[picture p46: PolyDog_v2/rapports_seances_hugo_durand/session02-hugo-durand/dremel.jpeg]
  
  <figcaption>Fastidieux mais assez bien précis au mm près</figcaption>
</figure>

J'ai lancé les impressions de la nouvelle patte qui 1.3 fois plus grosse que la version 1, et avec des engrenages plus puissant et plus stable :

<figure align="center">
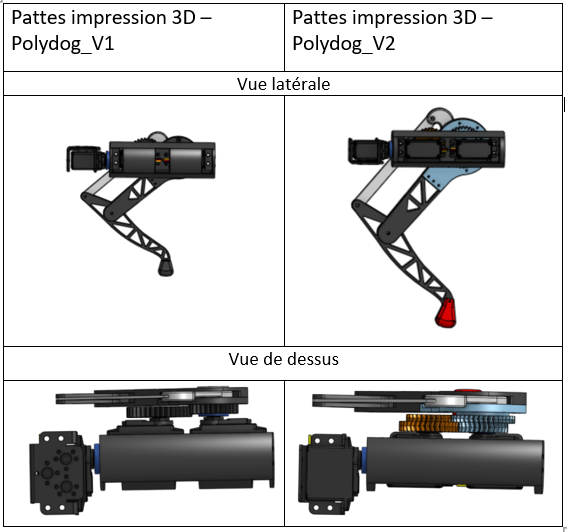
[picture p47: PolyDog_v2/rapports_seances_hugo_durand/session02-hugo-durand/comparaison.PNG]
  
  <figcaption></figcaption>
</figure>

J'ai également modifié les trous des vis, la taille des parties en rapport avec le palonnier des servos moteurs pour que tout puisse être assemblable.

J'ai modifié le pied de la patte :

<figure align="center">
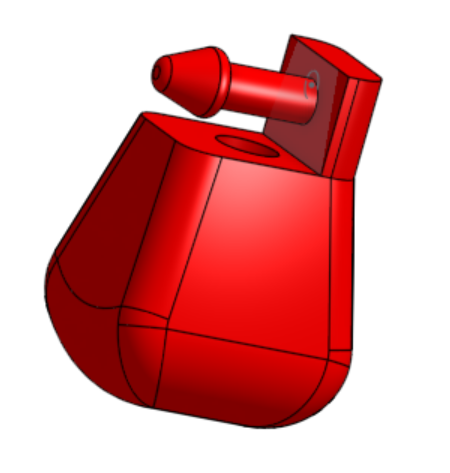
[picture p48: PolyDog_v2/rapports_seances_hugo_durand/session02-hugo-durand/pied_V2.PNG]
  
  <figcaption>L'embout rentre dans le tibia grâce à la matière flexible qui le compose</figcaption>
</figure>

J'ai crée cette pièce pour maintenir les roulements à bille dans l'encastrement des morceaux d'alu : 

<figure align="center">
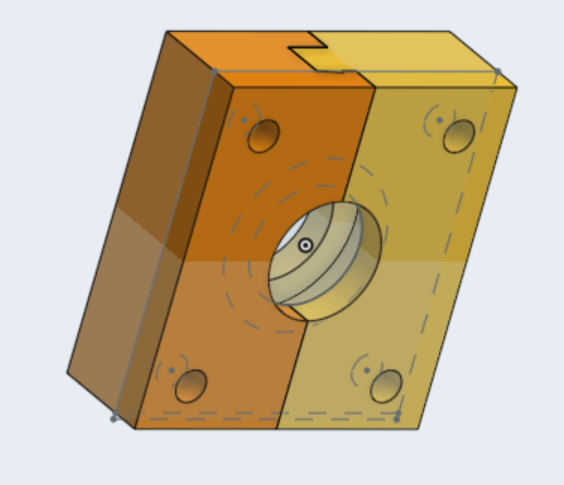
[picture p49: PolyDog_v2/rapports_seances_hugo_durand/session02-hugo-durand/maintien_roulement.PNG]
  
  <figcaption></figcaption>
</figure>

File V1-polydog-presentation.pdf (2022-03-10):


Peip 2 - Arduino | 2021-2022
ANJOU Raphaël - DURAND Hugo

DOG ROBOT

# POLYDOG

Project PolyDog

/ Prélude; Motivations, objectifs et problématiques; / Planning; Diagramme de Gantt et planning réel; / Hardware; Pièce 3D, vis, branchement électriques et composants; / Software; Algorithme principal, classes et méthodes; / SOMMAIRE


# MOTIVATION

### - Un robot qui se déplace - Un robot télécommandé - Une première dans l’école

/01

# OBJECTIFS ET PROBLÉMATIQUES

/01

/ Problématiques; / Objectif

Concevoir un robot chien qui :
● se déplace dans les 4
directions,
● est télécommandé.

● Quel système choisir pour le
déplacement d’une patte ?
● Quel degré de liberté de
chaque moteur ?
● Comment faire des mouvements
dans les 4 directions ?

# /02 DIAGRAMME DE GANT

/PORTABILITY; /EFFICIENCY

/CORRECTNESS
Venus is the second
planet from the Sun

/CLARITY
Mercury is the
smallest planet

Despite being red,
Mars is a cold place

# PLANNING RÉEL

/02

/LANGUAGE; /PROGRAM; /ALGORITHM

Mercury is the
closest planet to
the Sun and the
smallest one

Venus is terribly
hot and is the
second planet from
the Sun

Despite being red,
Mars is actually a
cold place full of
iron oxide dust

# /03 FONCTIONNEMENT DE LA PATTE


## / Modèle du parallélogramme

## / Engrenages d’augmentation de l’amplitude du mouvement de la hanche

# /03 VUE ÉCLATÉE DU ROBOT


Lynxmotion SCC32; Servo moteurs; Télécommande IR; Arduino UNO; Pixy2; LISTE DU MATÉRIEL ÉLECTRONIQUE

CIRCUIT ÉLECTRONIQUE

# /04 CLASSES DU PROGRAMME

/ CustomServo; / Leg; / PolyDog

Permet de communiquer
avec le SSC32 en
indiquant seulement
un angle.

Permet de contrôler
chaque moteur d’une
jambe sans se soucier
des décalages.

les mouvements du
chien.

# ALGORIGRAMME

/04


● Objectifs remplis dans une certaine mesure; ● Nécessité d’aide sur certains mouvements pour alléger son poids; ● Démonstration avec la manette; CONCLUSION ET DÉMONSTRATION

/ PERSPECTIVES; Problème de surpoids et/ou de puissance des moteurs potentiellement.; Réaliser une nouvelle version avec des moteurs plus robuste.


# Merci de nous avoir écouté !

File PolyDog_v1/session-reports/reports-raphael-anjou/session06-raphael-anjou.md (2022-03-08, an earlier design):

# Séance 6 : 04/02/2022 -> 11/02/2022

## Test de résistance au poids

&nbsp;&nbsp;&nbsp;&nbsp;Nous avons posé quelques objets sur le robot lorsqu'il est en position debout afin de tester sa résistance.

Test poids sur le robot

## Description du code écrit

&nbsp;&nbsp;&nbsp;&nbsp;Le code évolue avec le projet pour répondre aux nouveaux
besoins que l'on rencontre, mais aussi pour simplifier son implémentation. Je
vais ici décrire l'état actuel du code, ainsi que son fonctionnement.

> Librairies créées

&nbsp;&nbsp;&nbsp;&nbsp;J'ai créé deux classes : `CustomServos` et `PolyDog`.
La première permet d'implémenter des méthodes pour controler plus facilement les
servos moteurs. Dans son état actuel il n'y a que très peu de différences avec
le module `Servo` mais je pense pouvoir la diversifier pour nous faciliter le travail dans certains cas. La seconde est très importante car elle permet de controler
le robot et implémente toutes les méthodes de mouvements de celui-ci.

> CustomServos

&nbsp;&nbsp;&nbsp;&nbsp;Cette classe est construire sur la classe `Servo` et son fonctionnement est très similaire.

- `CustomServos.CustomServos(pin)` : constructeur d'un objet, `pin` est le pin de control du servo moteur.
- `CustomServos.attach()` : permet d'attacher le servo moteur au pin spécifié dans le constructeur.
- `CustomServos.write(angle)` : appelle simplement `Servo.write(angle)`.
- `CustomServos.control_with_potentio(int pin_potentio)` : permet de controler le `CustomServos` actuel avec un potentiometre dont le pin est spécifié en argument.
- `CustomServos.control_two_with_potentio(CustomServos servo2, int pin_potentio1, int pin_potentio2)` : permet de controller le `CustomServos` actuel et un autre spécifié en argument. Les pins des deux potentiomètres doivent aussi être indiqués dans les arguments.

> PolyDog

&nbsp;&nbsp;&nbsp;&nbsp;Cette classe permet de controler tous les mouvements du robot.

- `PolyDog.PolyDog()` : constructeur d'un objet. Permet d'initialiser 12 `CustomServos`correspondant à ceux du robot. Les pins sont directement implémentés par défaut dans le constructeur pour éviter les erreurs.
- `PolyDog.start()` : permet de mettre le robot dans une position levée stable.
- `PolyDog.forward_leg(int leg_number, int step, int offset_hanche, int offset_genou)` : permet de faire bouger les servos de la jambe à une certaine position du mouvement pour aller de l'avant. `step` permet d'indiquer le moment désiré. Les deux offset permettent d'indiquer la différence d'angle par rapport à celui de départ. Dans notre cas, les jambes **A et D** ont besoin d'un offset de 180° par rapport aux jambes **B et C**. `leg_number` indique la jambe à controler. Dans notre cas : **1->A**, **2->B**, **3->C**, **4->D**.
- `PolyDog.hold_shoulders()` : permet de positionner les servos moteurs des épaules dans une position où les jambes sont perpendiculaires au sol. Cette méthode est appelée dans `PolyDog.start()` par exemple.
- `PolyDog.attach_all_motors()` : permet d'attacher tous les servos moteurs du robot. Cette méthode doit impérativement être appelée dans le `setup()` pour que le robot soit controllable.
- `PolyDog.move_forward()` : permet de faire avancer le robot en suivant le pattern précisé dans `PolyDog.forward_leg()`. Il est possible de mettre un décalage entre l'exécution des mouvements de chaque jambe ce qui donne l'impression de controler les mouvements simultanéments.

## Recherches d'une séquence de marche

&nbsp;&nbsp;&nbsp;&nbsp;Pour faire avancer notre robot, il est nécessaire de trouver une séquence de mouvement plus ou moins longue lui permettant de se déplacer. J'ai rencontré de grandes difficultés sur ce point là. En effet, il faut réussir à synchroniser les mouvements des jambes pour que le robot ne perde pas l'équilibre, réussir à lever suffisamment la perte pour qu'il avance mais pas trop pour qu'il ne tompe pas, réussir à répartir correctement le poids entre les pattes etc...  
&nbsp;&nbsp;&nbsp;&nbsp;De nombreux problèmes qui ont donc induits de nombreuses itérations du programme de mouvement en avant. J'ai essayé avec des séquences plus ou moins longues, une répartition temps en l'air / temps sur terre plus ou moins grande, ou encore avec des décalages entre les pattes différents. Le résultat n'est pas toujours pas concluant mais vous trouverez dans la section suivante toutes les illustrations du parcours de notre robot vers la liberté de mouvement.

## Parcours du robot en vidéos (Youtube)

[Deux jambes simultanéments](https://youtu.be/BQK5qwYhp8c)  
[4 jambes mais sur le dos](https://youtu.be/-I2CmnTHJ1Y)  
[Toute première marche](https://youtu.be/czDSCy8KdlA)  
[Même cycle de marche que la première fois, mais les branchements sont organisés](https://youtu.be/wdTeotGUBME)  
[Il rampe... mais rapidement !](https://youtu.be/WcdHqzSt2Vk)  
[Il marche ! (à peu près...)](https://youtu.be/P47AMKD66D0)  
[Lentement... mais sûrement... le PolyDog avance...](https://youtu.be/SjZvboL3cDo)  
(J'ai atteint la limite journalière d'upload sur Youtube donc je rajouterais les vidéos suivantes petit à petit)

## Problèmes d'alimentation

&nbsp;&nbsp;&nbsp;&nbsp;Nous avons rencontré de nombreux problèmes au niveau de l'alimentation. Tout d'abord, nous pensions que le problème venait de notre montage entre une _Arduino Mega_ et un _Shield Adafruit_ que nous avions et qui n'était pas adapté pour alimenter autant de servo moteurs. Nous avons donc ensuite refait tout le montage avec une autre carte Mega ne nécessitant pas de _Shield_ cette fois-ci.

AJOUTER UNE PHOTO DE LA CARTE V1  
AJOUTER UNE PHOTO DE LA CARTE V2

&nbsp;&nbsp;&nbsp;&nbsp;Le problème n'était toujours pas résolu donc nous avons mesuré la tension de notre montage. À notre surprise, celle-ci était de 3.5V au lieu des 5V nécessaire. L'alimentation fournissait belle et bien 5V, mais à l'entrée de la carte il n'y avait que 3.5V. Le seul coupable restant était notre cable d'alimentation.  
&nbsp;&nbsp;&nbsp;&nbsp;Nous avons donc coupé en deux le cable pour vérifié si la perte de tension venait ou non de ce problème. Avec maintenant une demi-longueur de cable branchée, nous avons 4.5V, ce qui est quasiment les 5V nécessaires.
&nbsp;&nbsp;&nbsp;&nbsp;Il est donc possible de plusieurs de mes algorithmes de mouvement n'est pas fonctionné du simple fait qu'il n'y avait pas assez de tension pour faire fonctionner correctement les servo moteurs...

&nbsp;&nbsp;&nbsp;&nbsp;Les problèmes ne s'arrêtent pas là puisque nous soupçonnons maintenant un problème en raison des branchemnent internes de l'Arduino. Il est possible que le 4.5V que nous avons est du mal à atteindre tous les moteurs.  
&nbsp;&nbsp;&nbsp;&nbsp;Aux grands maux les grands remèdes, seulement les pins de signaux sont branchés directement dans l'Arduino. Le **5V** et le **GND** sont branchés dans un domino d'un ancien _Shield_ qui lui-même est directement relié à l'alimentation. Ce système semble fonctionner mais nous attendons avec impatience une nouvelle carte dont le fonctionnement a été pensé pour utiliser autant de servo moteurs.

Bazar de cables

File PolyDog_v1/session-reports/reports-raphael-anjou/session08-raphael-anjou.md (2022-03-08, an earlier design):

# Séance 8 : 27/02/2022 -> 03/03/2022

## Refactoring et nettoyage de tout le code

&nbsp;&nbsp;&nbsp;&nbsp;J'ai nettoyé tout le code, enlevé les commentaires en trop, renommé des variables qui devaient l'être etc... Cela m'a pris un certain temps mais c'était nécessaire afin de pouvoir rendre un code propre.

## Documentation

&nbsp;&nbsp;&nbsp;&nbsp;J'ai fait la documentation de toutes les méthodes et toutes les classes du code. J'ai respecté les normes de documentation pour le C++, qui sont très proches de celles pour JavaDoc. Cela représente un assez gros travail mais permettra à un utilisateur ne connaissant pas le projet de le comprendre mieux que s'il n'y avait rien.  
&nbsp;&nbsp;&nbsp;&nbsp;Je n'ai pas inclus de screen de la documentation mais vous pourrez la voir dans chacun des fichiers du dossier suivant : [src](../src/SSC-32_servo-controller/src/)

## Copyright

&nbsp;&nbsp;&nbsp;&nbsp;J'ai rajouté une license Open Source (Apache 2.0) au projet. Celui-ci pourra donc être réutilisé par ceux qui le souhaitent.

> Copyright (c) 2022-2022. ANJOU Raphaël & DURAND Hugo  
> Licensed under the Apache License, Version 2.0 (the "License"); you
> may not use this file except in compliance with the License.
>
> You may obtain a copy of the License at
>
> http://www.apache.org/licenses/LICENSE-2.0
>
> Unless required by applicable law or agreed to in writing, software
> distributed under the License is distributed on an "AS IS" BASIS,
> WITHOUT WARRANTIES OR CONDITIONS OF ANY KIND, either express or implied.  
> See the License for the specific language governing permissions and
> limitations under the License.

## PolyDog circuit

&nbsp;&nbsp;&nbsp;&nbsp;J'ai réalisé tout le circuit électronique du robot. Je me suis servi de Google Drawing pour faire les cables. Ce travail est assez fastidieux mais le résultat est concluant.  
&nbsp;&nbsp;&nbsp;&nbsp;J'ai rencontré des difficultés pour comprendre le branchement ICSP entre la Pixy2 et l'Arduino UNO car un cable est fourni avec la caméra.

PolyDog Circuit

&nbsp;&nbsp;&nbsp;&nbsp;Voici les informations que j'ai utilisé pour le branchement entre l'arduino UNO et la Pixy2.

Pixy2 pin configuration
ICSP pin configuration

## Organigramme logique du main.cpp

&nbsp;&nbsp;&nbsp;&nbsp;J'ai construit l'organigramme du main.cpp de notre projet afin de l'inclure dans notre projet. Je dois me renseigner sur s'il est nécessaire ou non de faire le diagramme pour chaque méthode appelé dans le programme.

Diagramme logique main.cpp

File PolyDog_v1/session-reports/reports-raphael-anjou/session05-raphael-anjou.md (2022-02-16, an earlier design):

# Séance 5 : 14/01/2022 -> 03/02/2022

## Création d'un corps plus grand

&nbsp;&nbsp;&nbsp;&nbsp;Pour l'instant le corps est toujours en bois pour que
nous puissont tester l'équilibre du robot avec cette largeur avant d'un imprimer un en 3D. Nous avons
toutefois dû recouper au laser une v2 plus large que la v1, et prenant mieux en
compte les libertés des modules des pattes



## Installation des moteurs des épaules et des socles pour les différents axes.

&nbsp;&nbsp;&nbsp;&nbsp;Les moteurs sont fixés aux bois grâce aux socles fournis par M. Masson. Il a fallu percer le bois aux bons endroits pour que ceux-ci soit bien orienté. \
&nbsp;&nbsp;&nbsp;&nbsp;De plus, je me suis occupé de réaliser les socles qui reçoicent l'axe de l'épaule. Ceux-ci devaient être le plus précis possible afin de ne pas avoir de décalage entre l'emplacement du moteur et le trou pour l'axe.



## Installation des pattes

&nbsp;&nbsp;&nbsp;&nbsp;Installer les pattes n'étaient pas aussi facile que nous l'espérions. En effet, il faut bien placer nos pièces sur l'axe du servo afin que celle-ci est l'amplitude correcte de mouvement. \
&nbsp;&nbsp;&nbsp;&nbsp;J'ai donc testé chaque patte avec un petit programme permettant de bouger les servos avec deux potentiomètres.



## Première fois debout (!!!)

&nbsp;&nbsp;&nbsp;&nbsp;J'ai cherché les valeurs précises pour chaque servo afin que le robot puisse tenir debout, et nous avons réussi !



&nbsp;&nbsp;&nbsp;&nbsp;En revanche, on a quelques problèmes de tremblement probablement dû à un problème d'alimentation (malgré les 5V 30A théoriquement nécessaire).



## Finalement fonctionnel

&nbsp;&nbsp;&nbsp;&nbsp;Après modifications du branchement entre l'alimentation et l'Arduino MEGA, le robot a cessé de trembler !



## Visserie

&nbsp;&nbsp;&nbsp;&nbsp;Pas de photos pour cette étape malheureusement, mais avec Hugo nous avons placé toutes les vis nécessaires pour que notre robot tienne la route. En effet, avec seulement les vis que nous avions mises nous avions des problèmes de pièces qui ne tiennent pas ou se dévissent...

## Au niveau du code

&nbsp;&nbsp;&nbsp;&nbsp;L'écriture du code a évolué continuellement depuis le dernier rapport séance.

### PlatformIO

&nbsp;&nbsp;&nbsp;&nbsp;J'ai appris à utiliser PlatformIO afin de pouvoir uploader dans l'Arduino les programmes depuis Visual Studio Code. Nous utiliserons donc maintenant la structure des fichiers de PlateformIO. \
&nbsp;&nbsp;&nbsp;&nbsp;En revanche, l'arborescence du dossier `src` de notre projet n'est pas du tout optimale. Ranger tout cela est un des objectifs de la semaine.

[Emplacement du dossier PlatformIO](/src/LearningPlatformIO)

### Les classes

&nbsp;&nbsp;&nbsp;&nbsp;J'ai commencé à créer des classes en C++ pour notre projet afin de pouvoir controler les servos plus spécifiquement. Plus de classes verront le jour par la suite en fonction de nos besoins.

[Emplacement de la classe](/src/LearningPlatformIO/lib/CustomServos)

### Programme pour tester la rotation des servos

&nbsp;&nbsp;&nbsp;&nbsp;Ce programme permet de controller facilement deux servos simplement grâce à deux potentiomètres branchés sur le bloc de contrôle du robot.

[Emplacement du programme](/src/LearningPlatformIO/others/test-servo.cpp) #Deprecated

Link no longer available due to code modification.

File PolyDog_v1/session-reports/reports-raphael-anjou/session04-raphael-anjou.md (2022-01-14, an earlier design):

# Séance 4 : 06/01/2022 --> 13/01/2022

&nbsp;&nbsp;&nbsp;&nbsp;De gros progrès ont été fait au cours de la semaine. Nous avons donc quasiment fini la version
définitive de notre prototype de patte. Les éléments sur lesquels j'ai travaillé pour en arriver là sont détaillés 
ci-dessous.

### Prototype actuel de la patte :



### Révision du mécanisme

&nbsp;&nbsp;&nbsp;&nbsp;L'ancien mécanisme que nous avions créé était fonctionnel, mais ne nous permettait pas d'avoir
l'amplitude de mouvement dont nous avions besoin. Cela été dû à la réduction d'un engrenage a 25 dents vers un engrenage
à 40 dents. La solution a donc été de tout simplement agrandir l'engrenage directement relié au moteur et de réduire celui
accroché à la pâte. Ainsi, nous avons une bien plus grande amplitude du mouvement de la patte malgré la limite de 180° du
moteur.

### Nettoyage des pièces après leur impression

&nbsp;&nbsp;&nbsp;&nbsp;Le dur labeur de devoir nettoyer toutes les structures permettant l'impression des pièces 3D. Ce
n'est pas plus amusante des parties, mais elle est nécessaire et doit être faite correctement pour que le résultat soit de
qualité.



### Mise en mouvement des moteurs (utilisation d'un potentiomètre ou utilisation d'une séquence prédéfinie)

&nbsp;&nbsp;&nbsp;&nbsp;J'ai réalisé deux petits programmes (et réalisés leurs systèmes électroniques respectifs)
permettant la mise en mouvement des moteurs.

&nbsp;&nbsp;&nbsp;&nbsp;Le premier permet de manipuler les moteurs séparément avec leur propre potentiomètre. On peut
ainsi voir les limites des mouvements possibles, mais aussi récupérer des valeurs d'angle qui vont servir dans le second
programme.



&nbsp;&nbsp;&nbsp;&nbsp;Le second est tout simplement une suite de commandes que l'Arduino transmet aux moteurs. Cela
effectue un cycle afin qu'il s'exécute en continu. Le mouvement n'est pas celui que l'on utilisera pour la marche mais
donne une idée de ce que l'on peut faire.



### Corrections minimes concernant les pièces 3D

&nbsp;&nbsp;&nbsp;&nbsp;Nous avons fait plusieurs itérations des pièces de la patte dont Hugo a fait la majorité des
modélisations. Ces itérations nous ont notamment permises de corriger la taille de certains trous, leurs emplacements,
ainsi que la précision d'assemblage de certaines.

### Utilisation de Adafruit PCA9685 16-Channel Servo Driver

&nbsp;&nbsp;&nbsp;&nbsp;Étant donné que nous allons devoir connecter 12 servos moteurs à notre Arduino, M. Masson nous a
conseillé d'utiliser un module Adafruit qui permet de gérer jusqu'à 16 moteurs simultanément.

&nbsp;&nbsp;&nbsp;&nbsp;J'ai donc tout d'abord cherché la documentation du module afin de comprendre comme il fonctionnait
et comment je pouvais le brancher avec l'Arduino. Simultanément je suis tombé sur un bout de code permettant de faire une
première utilisation du module Arduino et découvrir ses méthodes. Une fois les branchements réalisés plus ou moins 
correctement après de multiples essais, mes deux moteurs étaient enfin opérationnels.



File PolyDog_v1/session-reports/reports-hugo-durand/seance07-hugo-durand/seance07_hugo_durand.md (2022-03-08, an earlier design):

# Séance du 23/02/2022

## Adaptation du code pour le nouveau controleur de servo moteur

Pour envoyer une commande à un servo branché sur le pin 4, pour qu'il aille à un angle de 90 degré en 500 millisecondes, on écrit :
```c++
//Code en Arduino
#4P1000T500;
```

1. ### `CustomServos`

De plus, dans la classe CustomServos, nous n'avons plus la nécessité d'attacher les servos à un pin particulier (~~servo_lambda.attach(4)~~).

J'ai alors modifié la classe CustomServos en y ajoutant les fonctions suivantes :

```c++
void CustomServos::move(int position, int time)
{
  Serial.print("#");
  Serial.print(this->_pin);
  Serial.print(" P");
  Serial.print(position);
  Serial.print(" T");
  Serial.println(time);
  delay(time);
}

// Modification de la fonction write, pour que l'on puisse garder notre code avec des angles compris entre 0 et 180 degré, par comodité

void CustomServos::write(int angle)
{
  this->move(map(angle, 0, 180, 500, 2500), 0);
}
```

## Problème de réglage

1. Nous nous sommes rendu compte que le servo controller n'était pas autonome et ne pouvait pas stocker en mémoire les commandes. Nous avions donc besoin d'une carte Arduino pour faire l'intermédiaire et de transmettre les infos sur le serial;

Voici le montage :

<figure align="center">
  
</figure>

2. Ensuite, deuxième soucis, le code se transférait successfullement sur la carte UNO mais cette dernière ne relayait pas l'information au servo controller. Les led RX et TX demeuraient éteinte. Après des heures et des heures de recherches en vain, il suffisait en réalité de recréer un projet sur PlateformIO et de transférer le code, et ça a marché.

## Impression des pièces

En mettant la pièce des côtes du bas dans le slicer de l'imprimante, le poids serait de 230gr, je l'ai donc modifié ainsi avant impression :

<figure align="center">
  cote plus légère.png
</figure>

J'ai modifié également les bras de maintien des épaules (ou plus logiquement la colonne vertebrale), en y perçant son centre :

<figure align="center">
  trou au centre.png
</figure>

J'ai rajouté également deux clips pour les cables pour tester si cela fonctionne mais pour le moment j'en suis pas très convaincu.

## Assemblage du nouveau corps

Nous avons commencé par insérer des insert dans le nouveau corps, une étape délicate, qui n'a pas été filmé. Le principe est de faire chauffer le plastique autour de l'insert avec une panne de fer à souder. L'insert descend dans la matière plastique jusqu'à ne plus dépasser de la surface. Il faut être très attentif à ce que l'insert se place droit et qu'il ne soit pas décalé, sinon la vis ne rentre pas :

<figure align="center">
  
</figure>

Puis nous avons démonté l'ancien corps de robot pour y extraire les 4 pattes :

<figure align="center">
  
</figure>

Lorsque j'ai pu assemblé la pièce 3D des côtes du bas et le ssc32-servo controller, j'étais très content parce que l'emboîtement s'est fait parfaitement :

<figure align="center">
  
</figure>

Nous avons ensuite continué l'assemblage entre les deux pièces qui viennent maintenir les boitier de servo-moteurs que j'appelle les bras avec les côtes du bas et le support de fixation des moteurs centraux. Nous avons dû bien évidemment poncer certaines surface de pièce 3D. J'ai oublié de prendre en compte la marge d'erreur de l'imprimante 3D qui est de environ 0.4 mm. Cette imprecision reportée sur plusieurs couche de matière entraîne des écarts de 1.3 mm :

<figure align="center">
  
</figure>

## Problèmes rencontrés

Premier soucis : mettre les insert dans le corps nous a été très compliqué, nous avons eu beaucoup d'erreur. 

Nous avons pu les résoudre en retouchant l'insert et en refondant le plastique pour replacer convenablement l'insert. Parfois, nous avons dû grossir le trou de la vis pour que l'alignement entre le pas de vis et l'insert soit plus optimal.

Deuxième soucis : nous avons cassé à moitié le bras orange au niveau où on place les vis parce que le design à ce niveau n'est pas assez épais. Avec un peu de colle ultra-forte, le problème est contourné. Les vis qui viennent maintenir l'ensemble renforce sa solidité.

<figure align="center">
  
</figure>  

Troisième soucis : nous avons cassé une autre pièce du montage, les côtes du bas.

 Explication : nous avons placés un insert sur un endroit délicat et pas très épais.
 
  Nous avons visser l'ensemble pour tester le pas de vis, mais en dévissant pour continuer le montage, l'insert n'était plus bloqué dans le plastique, on a donc forcé dessus pour faire sortir la vis. Un bout de la pièce est venu avec la vis. Mais c'est pas grave, une fois l'ensemble vissé ce n'est pas très génant :

<figure align="center">
  
</figure>

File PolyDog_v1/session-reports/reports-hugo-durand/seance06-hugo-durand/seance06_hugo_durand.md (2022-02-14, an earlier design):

# Séance du 09/02/2022

## Agencement et calibration des pattes

La séance dernière, nous avions quelques soucis sur l'uniformité des angles de chaque patte. 

<figure align="center">
  
  <figcaption>les servos moteurs passent de 0° à 180° de la même façon.</figcaption>
</figure>

Nous avons donc placé la patte en position couché (le point minimum, la patte ne peut pas aller plus loin). Nous avons calibré le servo_genou à 90° (pour se lever le genou doit pouvoir aller dans les deux sens) et le servo_hanche à 180°.

Je me suis occupé de démonter de nouveaux les servos moteurs. On a lancé un code qui permet au chien de se maintenir debout. Ensuite, on assemble les pièces d'une patte en modifiant son degré de liberté légèrement pour que cette dernière vienne se calibrer avec les autres pattes. A la fin, notre robot se tient beaucoup plus droit.

## Premier pas sur la terre ferme

En étudiant le mouvement relatif d'une patte comme nous le percevons visuellement, nous en avons extrait les angles associés à chaque étape de la marche. Raphael a passé une longue nuit a optimisé ce mouvement :

<figure align="center">
  
</figure>

Au sol, il réalise ce déplacement : 

<figure align="center">
  
</figure>

Ensuite, Raph a optimisé le système pour que les pattes avancent en simultané avec un décalage de mouvement. Autrement dit, la patte A fait 1-2-3-4, la patte B fait 2-3-4-1 et ainsi de suite.

Pour le moment, nous en sommes arrivé à ceci :

<figure align="center">
  
</figure>

## Modélisation du corps

De mon côté, je me suis attelé à construire un corps de robot. 

Au début, nous avions une mega strong comme carte. La voici avec le bout du cable d'alimentation soudé :

<figure align="center">
  megastrong
</figure>

J'ai du rechangé tout le corps par le suite, avec la nouvelle carte de plus grande dimension : 7,62 x 5,84 cm (trous de montage à 0,38 cm de chaque bord). Nous avons alors revu la taille du robot et choisi d'augmenter la largeur pour que la carte puisse passer entre les moteurs de droite et de gauche. Il fera environ 17.6cm de large sur 42cm.

J'ai commencé par créer la plaque qui relie les 4 servo_moteurs des épaules. Le trou au milieu est pour laisser de la place à la carte fixé sur le dessus du corps

<figure align="center">
  plaque verte
</figure>

Puis, je voulais que les cotes du bas englobe les moteurs avec une forme qui ressemble à un corps en chair et en os, qui épouse la forme d'une cage thoracique :

<figure align="center">
  cote du bas
</figure>

Ensuite, comme on remarque sur le dessin, mon souhait était de centralisé le corps sur les moteurs des épaules. J'ai d'abord pensé mettre la carte arduino la tête en bas en la fixant sur le dessus du corps.

Mais finalement, en extrudant, la carte peut se fixer convenablement et cela sera plus pratique pour brancher les fils:

<figure align="center">
  cote du bas
</figure>

Le dessus du corps pour cacher tous les fils qui dépasse :

<figure align="center">
  carapace
</figure>

Enfin j'ai réalisé les bras de corps pour relier le corps principal au embouts des boitiers aux extremités. J'ai pas mal galéré sur ce dernier en utilisant la fonction loft, le prévoir assez grand pour que l'on puisse se permettre de faire un trou à l'intérieur et y glisser les cables d'alimentations :

<figure align="center">
  bras
</figure>

Après beaucoup de recherches pour de meilleures fixation et d'optimisation de design, je suis fier de vous présenter la version finale 1 du corps :

<figure align="center">
  robot
</figure>

Il sera encore sujet à modification. Mais je pense que globalement celui-ci et pas mal. Je vais voir avec Xavier pour les fixations entre les différentes pièces, de la meilleure chose à faire pour tout soit solide.

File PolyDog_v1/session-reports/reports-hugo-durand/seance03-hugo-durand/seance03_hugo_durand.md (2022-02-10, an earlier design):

# Séance du 06/01/2022

J'ai continué pendant les vacances l'assemblage des pattes. J'ai incorporé le troisième moteur au reste du module de la patte. Je me suis rendu compte que les 4 pattes ne seront pas les mêmes. J'ai dû appliquer un miroir à certaines pièces et assembler les moteurs de manière différente pour que l'ordre des 3 moteurs soit les mêmes.

Petit aperçu de l'assemblage des pattes ensemble pour obtenir des idées de corps :



Je les ai ajouté dans un assembleur le robot complet, mon principale soucis maintenant etait de prevoir assez de place pour la carte Arduino et les batteries. J'ai testé certaines distances, j'ai pris 10 cm de largeur pour commencer :



J'ai créé un corps en contexte, j'ai eu un peu de mal a comprendre le concept sur Onshape pour créer une pièce à partir d'un assemblage. Mais finalement c'est ultra pratique pour etre précis.

J'ai pris la fantaisie d'essayer de rendre le robot un peu plus esthétique, en imaginant un squelette de chien, avec des cotes comme cage de protection des appareils électronique. Mais c'est prévoir beaucoup de poids pour pas-grand-chose, j'ai mis en suspens l'idée. Raphael m'a dit que ce n'est pas biologiquement correcte, parce que les cotes d'une cage thoracique sont autour du corps et pas au-dessus. La contrainte c'est que si je centralise la cage thoracique, cela gênera le mouvement des pattes.



Pour le mouvement de la patte, on utilise, un engrenage entre le pignon du moteur et le pignon de la hanche. J'ai modélisé les deux pièces pour que l'une et l'autre soit en accord. En début de séance, je suis allé les imprimer en 3D. Vers 12 h, je les avais en main, ça marche parfaitement, je suis content.



J'ai testé les servo-moteurs, je l'ai ai fait tourner avec un petit code. Je me suis rendu compte que j'ai 2 types de moteurs : continus et non-continu. Sauf que je souhaite plutôt obtenir des moteurs non-continu, qu'ils se rendent à l'angle demandé et s'arrêtent. J'ai changé et j'ai maintenant 3 moteurs MG 996R avec les mêmes embouts ciculaire.

J'ai dû changer tous les engrenages et les trous des pièces modelisée pour que le robot soit mis a jour. Voici ma patte après de nouvelles modifications :



Le vendredi 7/01 : Je continue les détails de modelisation pour que la patte soit prête pour impression. Cette pièce a été modifié parce que les trous pour la vis étaient trop proche et allaient frotter avec la pièce pendant le mouvement :



J'ai envoyé un mail a Frederic Juan pour impression et la suite sera détaillé dans le prochain rapport de séance.

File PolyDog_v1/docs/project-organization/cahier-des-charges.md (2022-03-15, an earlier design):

# CAHIER DES CHARGES FONCTIONNEL DU ROBOT

## Présentation générale du projet

#### &nbsp;&nbsp;&nbsp;Inspiration

&nbsp;&nbsp;&nbsp;&nbsp;&nbsp;&nbsp;&nbsp;&nbsp; Au commencement, nous avons fait pleins de recherches sur les projets qui ont déjà été fait pour nous inspirer et avoir un aperçu de ce qui serait faisable de créer.

Nous nous sommes vite orientés vers un robot arduino qui se déplace, notamment avec un certain équilibre. On s'est alors penchés sur le robot Spot de Boston dynamics, puis sur le chien Bittle de Petoi, Spot Micro et Mini Pupper.

#### &nbsp;&nbsp;&nbsp;Objectifs du Projet

&nbsp;&nbsp;&nbsp;Nous souhaitons créer un robot chien, son nom est PolyDog, une structure plastique montée sur quatre pattes articulées. Il sera télécommandé par une manette xbox en bluetooth.

### &nbsp;&nbsp;&nbsp;Fonctionnalité de PolyDog

* Marcher dans les 4 directions
* Combinaison de commande pour faire certaines actions préprogrammées du robot.
* Rotation sur lui-même

### &nbsp;&nbsp;&nbsp;Étape de la réalisation du projet

- [ ] Modélisation 3D du robot
- [ ] Choix du Moteur(s) et des modules Arduino
- [ ] Construction d'une patte et essai de son bon fonctionnement
- [ ] Assemblage du corps et des 4 pattes
- [ ] Gestion de l'équilibre de son buste
- [ ] Connecter la manette à notre robot chien
- [ ] Automatisation des mouvements du robot par de multiples commandes de la manette
- [ ] Essais et corrections des bugs

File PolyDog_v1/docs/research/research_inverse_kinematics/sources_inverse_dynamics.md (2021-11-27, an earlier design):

### Research about the inverse dynamics method

> **Definition :**
> Abstract. Manipulator inverse dynamics, or simply inverse dynamics, is the calculation of the forces and/or torques
> required at a robot's joints in order to produce a given motion trajectory consisting of a set of joint positions,
> velocities and accelerations.

> **Forward or inverse dynamics ?**
> 
> **This is an extract from the file inverse_vs_forward_dynamics**
> 
> The results of this work indicate that direct transcription
> implementations relying on forward dynamics to define the
> defect constraints can be reformulated with inverse dynamics
> to see an increase in performance, for both feasibility or minimization problems, and without sacrificing the feasibility
> of the solutions to the optimization problem. An additional
> reason to prefer inverse dynamics is robustness to coarser
> discretizations, both in terms of computation efficiency and
> faithfulness of solutions with respect to finer discretizations.
> When minimizing a cost function, the locally-optimal solutions computed with either formulation are essentially the
> same. However, when an objective function is not considered,
> the formulations may diverge to different solutions. Experimentally, we have observed that the solutions computed with
> inverse dynamics are easier to perform in real hardware. The
> reasons behind this divergence are not yet clear to us, and
> this is something we plan to investigate in future work.
> Erez and Todorov [13] observed a striking feature in their
> results: an emergent coordination between legs and opposite
> arms during a running gait. In this work, for the humanoid
> jumping task, we also observed such emerging behavior:
> the resulting motions swing the arms upwards to build-up
> energy before the take-off instant. Both in [13] and our work,
> these features originated without any explicit modeling—
> reaffirming the power of dynamic trajectory optimization.
> In recent work [28], we took into account uncertainty and
> robustness to disturbances using direct transcription. Considering uncertainty usually incurs additional computational
> cost due to more complex problem formulations. With the
> findings from this paper, we plan to redefine the dynamics
> defect constraints in that work with inverse dynamics, improving the performance of our robustness framework and
> making it more competitive.

### Conclusion
We should consider inverse dynamics as it is said to be more efficient and easier to implement in robotic projects.

# IDEAS AND SOURCES

**Coding train videos**

[Coding Challenge #64.1: Forward Kinematics](https://thecodingtrain.com/CodingChallenges/064.1-forward-kinematics.html)
[Coding Challenge #64.2: Inverse Kinematics](https://thecodingtrain.com/CodingChallenges/064.2-inverse-kinematics)
[Coding Challenge #64.3: Inverse Kinematics - Fixed Point](https://thecodingtrain.com/CodingChallenges/064.3-inverse-kinematics-fixed-point)
[Coding Challenge #64.4: Inverse Kinematics - Multiple](https://thecodingtrain.com/CodingChallenges/064.4-inverse-kinematics-multiple)

**Complete tutorial creating a four legged robot with arduino #KITtyBot**

[Tutorial link](https://create.arduino.cc/projecthub/StaffanEk/kittybot-f21cc0)

**Others**

[General description about inverse dynamics](http://www.clinicalgaitanalysis.com/teach-in/inverse-dynamics.html)
File : humanoid_modeling_inverse_control.pdf
File : history_models_legged_robotics.pdf
[Overview of inverse dynamics](https://medium.com/unity3danimation/overview-of-inverse-dynamics-2ed60d0c37ef)
[Equations inverse dynamics](https://hackaday.io/project/21757-object-following-control-of-a-robotic-camera-arm/log/61689-inverse-dynamics-controller)
[Wikipédia : modélisation de robots (très complet)](https://fr.wikipedia.org/wiki/Mod%C3%A9lisation_des_robots#Mod%C3%A9lisation_cin%C3%A9matique_inverse)
File : robot_humanoide_ds_corrige.pdf

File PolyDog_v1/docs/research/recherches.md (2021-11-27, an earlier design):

Par exemple, dans notre cas, nous avons déterminé que les actionneurs avaient besoin d’un couple minimum de 20 Nm pour effectuer une démarche rapide et agile. 

 ## Choix des matériaux

* Je pense que l'on prendra l'option pièce 3D pour avoir une flexibilité dans le design de pièces légères déformables.

* La taille n'excedera pas les 40x25cm de dimension. Cela dependra de la taille de l'imprimante 3D.

## Choix des modules électronique

## Brainstorming robot

- [ ] Fonctionnalités
  - [ ] Marcher
  - [ ] Connecter à une télécommande par bluetooth
- [ ] Étapes
  - [ ] Faire un modèle (dessin ou 3D, etc.)
  - [ ] Réfléchir à l’électronique
    - [ ] Quels moteurs ?
    - [ ] Combien de moteurs ?
  - [ ] Faire les modules électroniques
  - [ ] Faire les programmes
    - [ ] Gestion des mouvements des jambes
    - [ ] Gestion de l’équilibre
    - [ ] Gestion de la vitesse
  - [ ] Designer les pièces
  - [ ] Créer les pièces
  - [ ] Assembler les pièces et les modules électroniques
  - [ ] Connecter la télécommande au robot (~50€ = manette Xbox)
  - [ ] Associer les boutons à certaines commandes

## Créer une librairie Arduino
[Lien](https://www.arduino.cc/en/Hacking/libraryTutorial)

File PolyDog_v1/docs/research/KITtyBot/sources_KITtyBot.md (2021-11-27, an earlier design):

### Opensource project #KITtyBot

[Arduino Project Hub](https://create.arduino.cc/projecthub/StaffanEk/kittybot-f21cc0)

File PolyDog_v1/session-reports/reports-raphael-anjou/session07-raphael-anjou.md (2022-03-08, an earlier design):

# Séance 7 : 12/02/2022 -> 26/02/2022

## Encore des tests de marche infructueux

&nbsp;&nbsp;&nbsp;&nbsp;Je pense qu'on aurait pu faire un long métrage si on avait filmé tous les échecs de marche avant pour le robot... En voici l'un deux :

[Échec marche avant]()

## Marche synchronisée

&nbsp;&nbsp;&nbsp;&nbsp;Nous sommes rassuré par le fait que nous arrivions à faire bouger toutes les jambes de manière synchronisée et identique. Mais le robot ne marche toujours pas...

Jambe synchronisé

## Nouveau corps pour le robot

&nbsp;&nbsp;&nbsp;&nbsp;Nous avons passé beaucoup de temps au FabLab pour mettre en place le nouveau corps de notre robot.

Comme d'habitude, il a fallu d'abord nettoyé toutes les pièces imprimées en 3D...

Nettoyage pièces

Nous avons ensuite démonté les 4 pattes du robot de l'ancien corps qui était en bois.

Robot démonté

C'était un petit peu le bazar sur l'établi...

Etabli en bazar

Je n'ai malheureusement pas retrouvé les vidéos concernant cette partie là du projet. Avec Hugo, nous avons mis en place plusieurs inserts dans les pièces 3D afin de pouvoir les viser ensemble sans risquer de casser le plastique. Il a fallu utiliser le fer à souder pour faire fondre le plastique autour du trou pré-existant, et ensuite rentrer l'insert dedans.

Le robot commence à prendre forme.

Robot en cours de construction 01

Robot en cours de construction 02

![Robot design final]() // TODO : Demander une photo à Hugo du design final

## Rush final avant la Journée Porte Ouvertes

&nbsp;&nbsp;&nbsp;&nbsp;Malgré le fait que je sois positif au covid, donc confiné, donc ne pouvant pas aller à la JPO, j'ai décidé de faire une nuit quasi blanche afin d'avoir un robot avec le plus de fonctionnalités possibles pour le lendemain étant que M. Masson pourra venir le chercher. J'ai travaillé quasi non-stop sur le robot de 14h (25/02) à 5h30 (26/02). Heureusement que j'avais du café...

_Photos prises à 23h30 ("seulement" 2 cafés déjà pris à ce moment là)_

Selfie nuit blanche

**Tous les éléments suivants ont été réalisés pendant ce rush.**

## Rajout de la classe `Leg`

&nbsp;&nbsp;&nbsp;&nbsp;J'ai fait cet ajout en début d'après-midi afin de nous simplifier la vie. Cette classe permet de stocker toutes les constantes pour les offsets des servos moteurs d'une jambe. Ainsi, peu importe la jambe, l'angle donné en input fera bouger chaque jambe au même endroit. Cette méthode gère aussi l'assignation des bons servos en fonction de la jambe choisie.  
&nbsp;&nbsp;&nbsp;&nbsp;Cela nous permettra par la suite de coder beaucoup plus rapidement les différentes méthodes dont nous avions besoin. Le code est aussi beaucoup plus propre que précédemment.

## Mise en place de la communication infrarouge

&nbsp;&nbsp;&nbsp;&nbsp;Grâce au module infrarouge et la télécommande que nous avons, j'ai pu les mettre en place afin de commander le robot à distance. J'ai donc du modifié le code du `main.cpp` pour qu'en fonction du bouton appuyé, cela appelle différentes méthodes.

Communication infrarouge

[Démonstration de la télécommande](link vers youtube pas encore mis car je n'ai pas les accès à la chaîne)

## Méthodes de mouvement

&nbsp;&nbsp;&nbsp;&nbsp;Cette nuit a été l'occasion de revoir toutes les méthodes de mouvement du robot. J'ai créé la méthode `excitement` qui permet au robot d'avoir une petite animation sympathique. J'ai ensuite beaucoup travaillé sur `move_forward`, `move_left` et `move_right`. J'ai testé beaucoup de valeurs différentes, des délais différentes, des ordres de mouvements différents.  
&nbsp;&nbsp;&nbsp;&nbsp;La méthode move_forward fonctionne quasiment même sans aider le robot en le tenant avec la corde. En revanche, les méthodes pour aller à gauche et à droite ne sont pas du tout optimisées ni fonctionnelles en réalité puisqu'il faut impérativement aider le robot pour qu'elles fonctionnent.
&nbsp;&nbsp;&nbsp;&nbsp;Vous pourrez trouver des vidéos des différents mouvements ci-dessous.

// TODO Mettre les vidéos sur Youtube mais je n'ai pas encore les accès.

[Il marche enfin !]()  
[Il marche mais avec de l'aide]()  
[Marche sur le côté avec de l'aide]()

## Pixy2

&nbsp;&nbsp;&nbsp;&nbsp;Cette nuit a aussi été l'occasion de brancher et utiliser la pixy2. J'ai rencontré quelques difficultés à la configurer correctement pour qu'elle suive les objets bleus. J'ai d'abord utilisé le logiciel **PixyMon** pour vérifier que cela fonctionnait correctement mais j'ai ensuite dû inclure le code qui permet à la caméra de suivre un objet grâce à son support.  
&nbsp;&nbsp;&nbsp;&nbsp;Le robot ne peut pas suivre un objet car il ne peut pas se déplacer sur le côté ni tourner. En revanche, il sait détecter lorsqu'un objet bleu est devant lui, si c'est le cas, il commence à marcher tout droit.

[Démonstration détection objet bleu]()

## Liste des vidéos qui vont être mis sur Youtube

- demonstration-infrarouge.mp4
- following-blue-square.mp4
- il-marche-enfin.mp4
- robot-ne-marchant-pas.mp4
- walking-forward-with-help.mp4

Ces vidéos sont dans le dossier : [ici](seance07_illustrations)

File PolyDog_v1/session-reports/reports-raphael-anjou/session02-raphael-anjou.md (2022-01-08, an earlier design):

# Séance 3 : 03/12/2021 --> 16/12/2021

Le temps que j'ai passé sur le robot a quasi intégralement était passé sur le mécanisme de la patte et de sa hanche.

### Placement des moteurs

J'ai utilisé des bouts de cartons et les moteurs que j'avais à disposition pour visualiser au mieux les différents moyens
de placer les moteurs pour que la patte fonctionne.

Après beaucoup de discussion avec Hugo et nos recherches, nous avons trouvé un modèle qui nous semble faisable. Et dont
le mécanisme se rapproche le plus de ce que nous avons en tête.



### Modélisation 3D

Nous utilisons OnShape pour la modélisation 3D.
J'ai modifié la pièce de la "hanche" et celle du "genou" pour correspondre à notre idée. 

##### Le genou 


#### La hanche


Enfin, j'ai commencé à assembler ensemble les moteurs et la patte. Je me suis rendu que faire notre propre support serait
plus facile pour placer les moteurs et éviter les erreurs.
J'ai donc utilisé un modèle 3D d'un socle "officiel" pour avoir les bonnes mesures et ainsi créer notre propre socle.

#### Socle personnalisé


#### Rendu actuel de la patte



#### Objectifs
Il reste encore des pièces à modéliser notamment pour connecter la hanche à l'un des moteurs. Il faut aussi mettre la place
le 3ème moteur dans le modèle 3D.
Une fois le modèle d'une patte modélisé nous pourrons le dupliquer pour les 4 pattes et ainsi commencer à faire la structure
de notre robot.

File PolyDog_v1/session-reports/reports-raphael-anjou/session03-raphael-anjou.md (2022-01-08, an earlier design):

# Séance 3 : 03/11/2021 --> 06/01/2022

Le travail que j'ai fait entre les deux dernières séances n'est pas très conséquent... J'ai tout de même travaillé sur
quelques points

### Design du robot

&nbsp;&nbsp;&nbsp;&nbsp;Nous avons beaucoup discuté avec Hugo de ce que l'on pourrait faire comme structure pour la partie
supérieure du robot. Hugo a donc proposé l'idée de faire des côtes sur le robot (cf. image). Je lui ai donc fait remarquer
que les côtes d'un chien n'était pas situé de cette façon. Notre design aurait donc montré une certaine ignorance concernant
l'anatomie d'un chien. De plus, cela aurait rajouté beaucoup de poids pas forcément nécessaire et déplacer le centre de
gravité du robot vers le haut. Ce décalage aurait eu pour effet de le rendre plus instable et la gestion de son équilibre
aurait été bien plus complexe.



### Assemblage du robot dans OnShape et création d'animation

&nbsp;&nbsp;&nbsp;&nbsp;Une fonctionnalité majeure de OnShape est celle des animations. Elle permet de voir les pièces
bouger et ainsi mieux comprendre les problèmes liés au design que l'on pourrait rencontrer. J'ai ainsi essayé pendant
plusieurs heures de gérer les relations entre les pièces, leurs contraintes et la façon dont elles intéragissaient entre
elles mais cela s'est révélé infructueux au niveau des engrenages. Je n'ai pas réussi à les connecter de tel sorte que
seulement la pièce de la patte concernée tourne en même temps que l'engrenage.

&nbsp;&nbsp;&nbsp;&nbsp;Le comportement actuel est démontré dans la vidéo ci-dessous. Le premier engrenage est censé déplacer
toute la patte en fonction de sa rotation. Ensuite, lorsque je sélectionne la pièce orange il faudrait seulement le "tendon"
et "tibia" se déplace (pièce bleu foncé et pièce très fine bleu ciel). Enfin, lorsque je sélectionne la pièce jaune de la
"hance" il faudrait que toute la patte bouge sans que la pièce orange ni le "tibia" ni le "tendon" ne bouge.



### Prochain objectif

&nbsp;&nbsp;&nbsp;&nbsp;Mon prochain objectif est d'écrire un petit bout de code pour qu'on puisse tester la patte avec
des moteurs une fois qu'elle sera imprimée en 3D. L'impression a été lancée vendredi donc nous pourrons la récupérer dès
le lundi 10/01/2022.

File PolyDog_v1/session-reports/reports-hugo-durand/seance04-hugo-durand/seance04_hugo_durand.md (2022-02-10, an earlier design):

# Séance du 13/01/2022

Nous avons récupéré nos pièces au fablab le lundi matin. Nous avons commencé à nettoyer les pièces, en grattant les renflements remplis de plastique.



Pas une mince affaire !

## Premier assemblage de la patte version1

Les moteurs rentrent pile poil à l'intérieur du boitier de la patte. C'était nickel.

Nous avons assemblé le tout au fablab avec les vis et écrous adaptés. Nous avons omis de faire un trou pour la vis du milieu pour l'embout qui se fixe sur l'axe de rotation du moteur. Un coup de perceuse et ni vu ni connu.

On avait hate de commencer à pouvoir bouger la patte avec un petit code de fortune et voir comment tout cela se comporte :



J'ai lancé un code avec deux angle 170 et 10 degré. Sauf que je me suis rendu compte rapidement que ce n'était pas un réel 180 degré de liberté, puisque la transmission de l'engrenage avec un pignons 25 dents vers un de 40 dents, me donnait un max de 90 degré de liberté.

Extrêmement déçu, deux solutions, obtenir un moteur 360, ce qui me permettait de ne pas chambouler toutes les pièces déja imprimé ou remodeliser pour équilibrer le nombre de dents de chaque coté. 

## Impression et assemblage de la patte version2

Etant impossible la première option, j'ai modifié les pièces pour réduire le pignon. Placé les trous pour les vis sur le bord exterieur : 



Nous avons réimprimer toutes les pièces impactés par le changement le mercredi matin. 

Jeudi matin nous avons de nouveau décortiqué les pièces. Assemblé. Vissé. 

## Correction d'un léger soucis

De nouveau, un léger problème, j'avais fait en sorte que le frottement entre le genou et la hanche soit minimum, seulement, a la fin la hanche était trop movible lateralement. J'ai augmenter le diamètre du cercle du genou pour eviter ce problème :



## La patte est prete

Nous sommes fier de vous présenter :



Cela marche, on se laisse une journée pour effectuer des test, Raph se lance dans le code, il s'assure que rien ne cloche. 

Pendant ce temps, je suis allé couper a la scie, les bout de barre de fer, qui serviront de maintient du boitier de la patte, comme ci dessous :



J'ai pu recuperer egalement 12 moteurs MG9996 flambant neuf :



Nous lancerons l'impression des autres pattes très prochainement, peut être demain.

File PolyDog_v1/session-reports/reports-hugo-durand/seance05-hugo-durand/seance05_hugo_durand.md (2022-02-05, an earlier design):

# Séance du 02/02/2022

## Two weeks ago

Il y a deux semaines, nous avons imprimés les 3 autres pattes. Nous avons eu quelques soucis sur certaines qui ont ont souffert pendant l'impression. Nous avons du les refaire. Nous avons pris un peu de temps à enlever toutes le plastique d'impression autour.

## One week ago

Nous avons créer un fichier svg pour découper avec l'imprimante lazer, les contours du corps provisoires. Nous y avons visser 4 bout de bois aux extremités du corps pour raccorder les boitiers. 

Nous avons montés le robot en entier avec les 4 pattes rattachés aux boitiers des servo-moteurs. 



Nous avons testé les 4 pattes en même temps, voir le fonctionnement des servos. Il était secoué de spasmes et de baisse d'énergie soudaine. Plus tard on a compris que c'était l'adaptateur Mac de Raph et les petits fils raccordés entre l'alimentation et les servos.

Plus tard, pendant les vacances, j'ai modéliser des pieds. Je l'ai imprimé avec du plastique plus élastique, pour obtenir une certaine adhérence au sol.



## Séance 5 

Pendant la séance, j'ai changé un moteur défectueux au niveau de l'épaule droite avant. J'ai galéré un peu à dévisser les vis à l'interieur du boîtier comme d'habitude.

Raph s'est occupé de trouver une formule de calcul des angles. On souhaiterait que le robot se lève droit.

## Le lendemain

Lors du montage des pattes, nous nous sommes dit que visser la totalité des vis n'étaient pas nécessaires vu la force des moteurs ça ne bougera jamais. 

Pourtant les écrous de certains assemblage partent très facilement, nous avons du tout démonter pour les ajouter. Ajouter des boulons pour plus de stabilité des moteurs dans leur boitier.

Etant donnés que nous n'avons pas correctement designé le boitier des pattes, on a du mal à insérer des écrous dans certains endroits. 

A la fin nous avons réussi. Le code n'est pas encore fonctionnel. Bien que nous avons fait très attention, à remettre les pattes aux mêmes amplitudes de liberté des servo-moteur. Lorsque l'on indique un angle, on obtient pas le même paterne entre les pattes.

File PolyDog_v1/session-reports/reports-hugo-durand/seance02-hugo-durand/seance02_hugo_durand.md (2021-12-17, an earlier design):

# Séance du 15/12/2021

## Mise au point avec Raphael :

Nous avons décidés de la manière dont nous allons assemblés les moteurs ensemble. Nous avons 3 moteurs : un pour le mouvement du genou, un pour lever la patte, un dernier pour rentrer ou écarter la patte du corps. 

On opte pour ce système :

<figure align="center">
  image du système vue de dessus
  <figcaption>image du système vue de dessus</figcaption>
</figure>

<figure align="center">
  image du système vue de cote
  <figcaption>image du système vue de dessus</figcaption>
</figure>

Le premier servo-moteur est relié au sommet du femur pour activer le genou.

Le deuxième est relié sur le contour du haut du femur avec un mecanisme d'engrenage.

Le troisième bouge le boitier de l'épaule lateralement.

On s'est concertés pour être au point à la rentrée des vacances :

- La modélisation et les pièces du robot chien sont entièrement terminés et prêtes pour impression à la rentrée.

- Modélisation des pièces sur notre logiciel de simulation. Cette partie ne devrait pas prendre trop de temps vu que on a juste à les importer sur le logiciel.

- Tester certains mouvement du robot sur la console : écrire un code qui bouge la patte dans un premier temps

## Recherche du meilleur logiciel de simulation :

On doit entraîner notre robot via une interface pour tester son poids par rapport à la force du moteur. Tester les rotations et les limites des mouvements des pattes. On aura la possibilité de tester notre code directement sur l'interface.

### Unreal Engine :

Ce logiciel est très connu et facil d'accès pour les débutants. Il utilise BluePrints : un système de script visuel, relier des blocks les uns avec les autres et créer un jeu d'éléments. Je me suis pas plus attardé sur ce logiciel, je me suis tout de suite tourné sur Unity parce qu'il est adopté par la plupart des dog robots développeurs open source.

### Unity :

J'ai testé Unity sous conseil d'un ami. Je l'ai installé et découvert un peu ses fonctionnalités. Il est composé d'un onglet mise en scène, vue d'une camera, un inspector, une console, une fenêtre pour y glisser les fichiers Obj. Point noir de ce logiciel : Le code est en C et je ne connais pas ce language. Pour pouvoir coder en Python, il faut installer une extension (je n'ai pas encore tester).

### Webot de Cyberrobotics :

Le téléchargement à mis trop de temps je n'ai pas pu le télécharger. En faisant quelques recherches : Webots est un simulateur open-source de robotique. Il est utilisé dans l'industrie, dans la recherche et éducation.

Parfait pour nous en tant qu'étudiant. Il existe également des exemples de simulations de Robot qui nous sont accessibles sur le site, pour avoir un aperçu de notre tache.

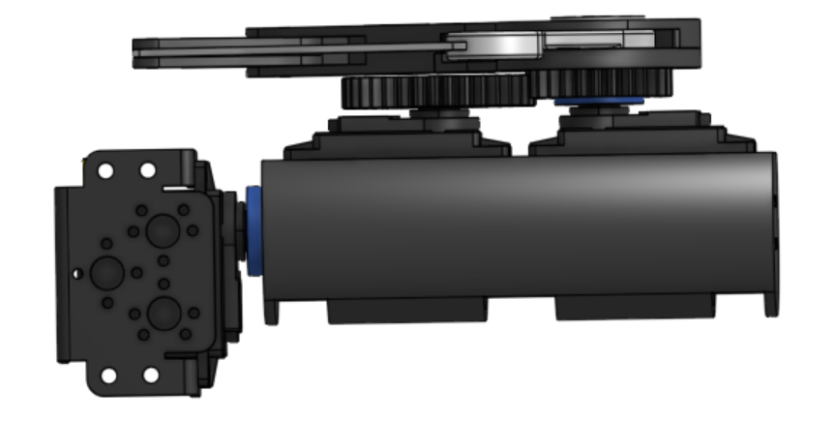
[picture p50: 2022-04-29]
PolyDog_v2/rapports_seances_hugo_durand/session02-hugo-durand/patte_v1_dessus.PNG

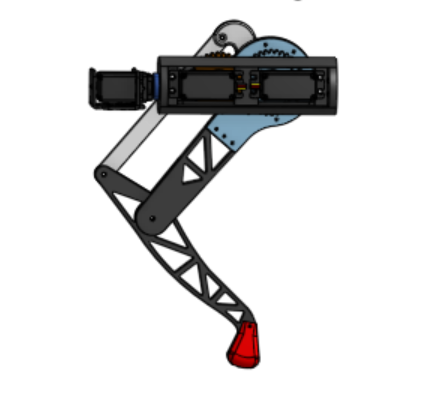
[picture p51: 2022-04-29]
PolyDog_v2/rapports_seances_hugo_durand/session02-hugo-durand/patte_v2_cote.PNG

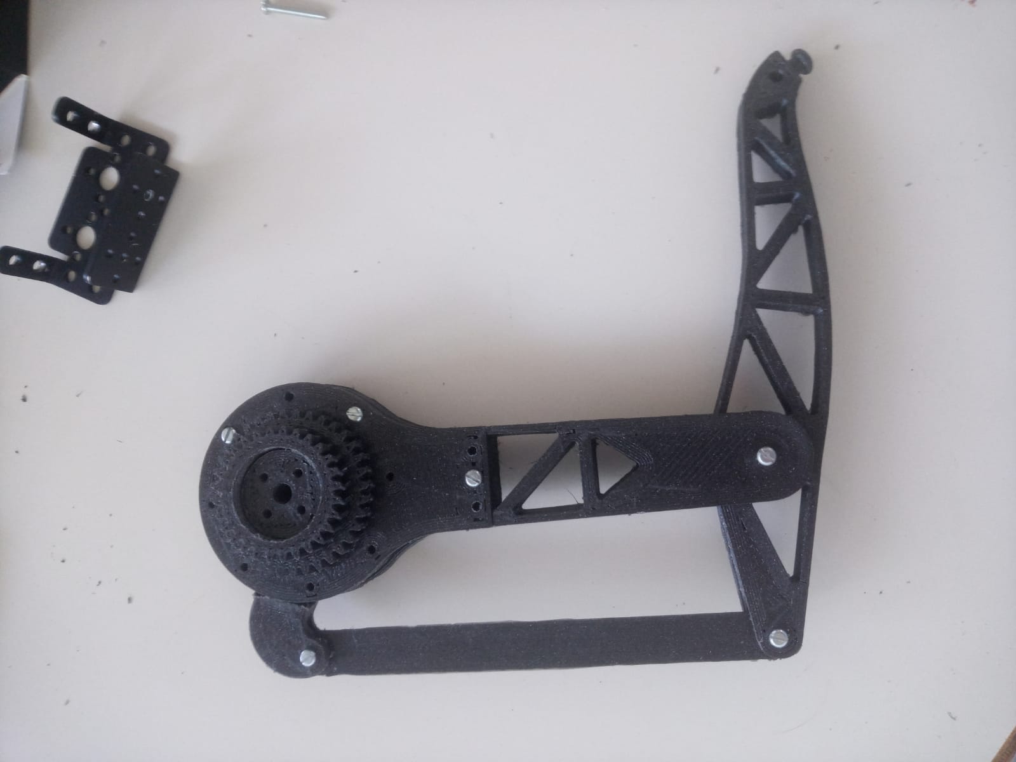
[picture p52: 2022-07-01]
PolyDog_v2/rapports_seances_hugo_durand/seance04_hugo_durand/patte_v2.jpeg

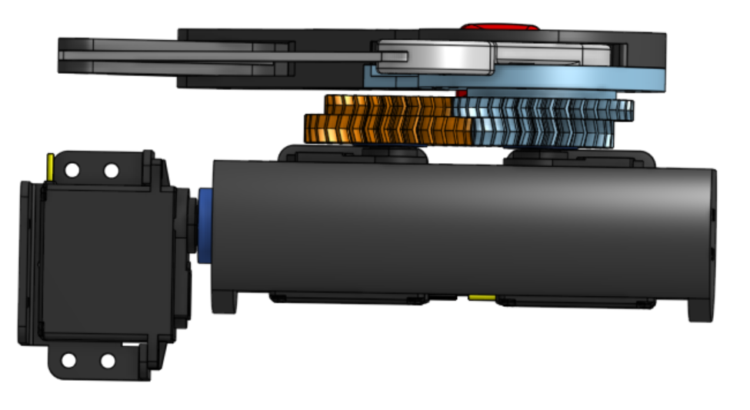
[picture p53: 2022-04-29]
PolyDog_v2/rapports_seances_hugo_durand/session02-hugo-durand/patte_v2_dessus.PNG

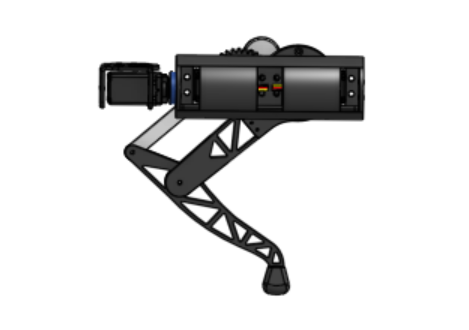
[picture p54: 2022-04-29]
PolyDog_v2/rapports_seances_hugo_durand/session02-hugo-durand/patte_v1_cote.PNG

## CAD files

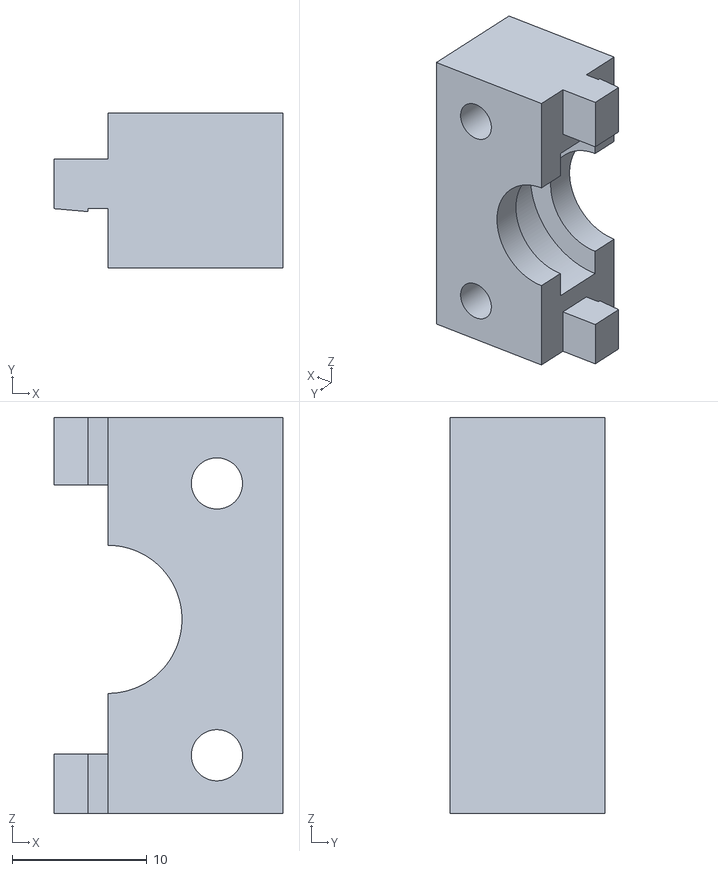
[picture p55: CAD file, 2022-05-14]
PolyDog_v2/3D-PRINTED-PART/maintien roulement v2 - Part 2.stl
17.0 x 11.5 x 29.4

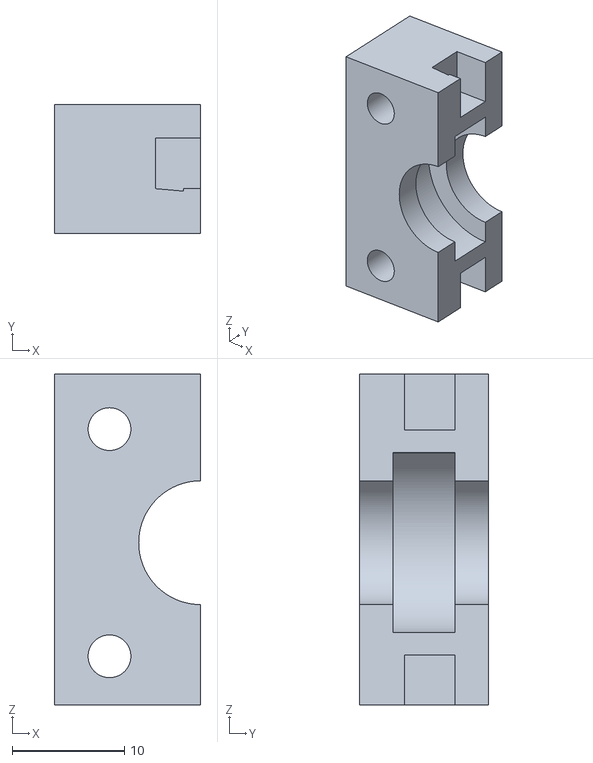
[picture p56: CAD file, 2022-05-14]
PolyDog_v2/3D-PRINTED-PART/maintien roulement v2 - Part 1.stl
13.0 x 11.5 x 29.4

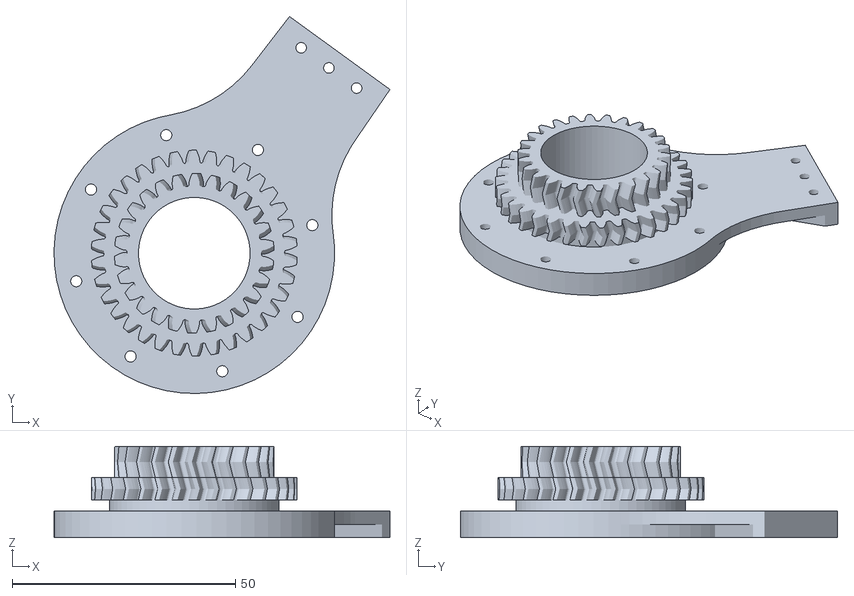
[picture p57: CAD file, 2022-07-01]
PolyDog_v2/3D-PRINTED-PART/Left_side_pieces/hanche cran v2 gauche --.stl
75.3 x 84.5 x 20.4

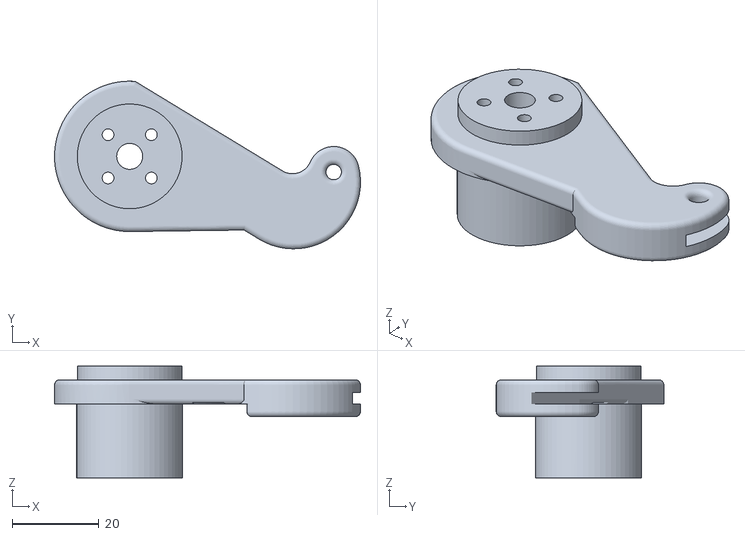
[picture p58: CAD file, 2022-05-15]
PolyDog_v2/3D-PRINTED-PART/Right_side_pieces/genou v2 droit- xx2.stl
70.7 x 38.7 x 25.8

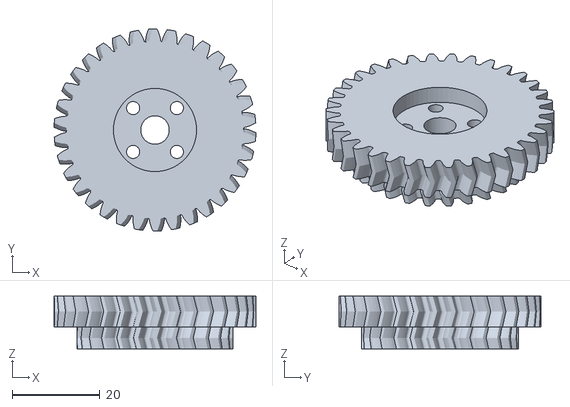
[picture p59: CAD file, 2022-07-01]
PolyDog_v2/3D-PRINTED-PART/v2-engrenage 1 accessoire --.stl
46.1 x 46.2 x 12.0

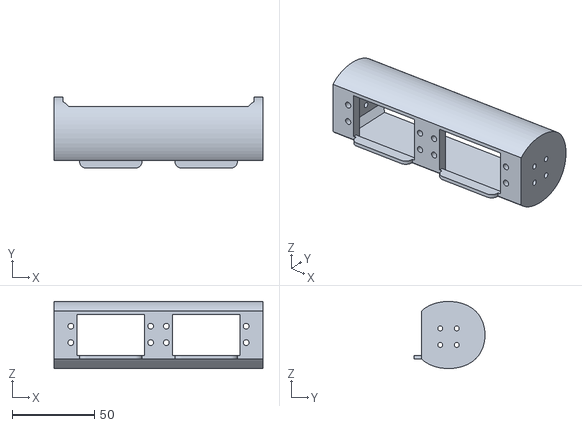
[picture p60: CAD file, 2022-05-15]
PolyDog_v2/3D-PRINTED-PART/boitier v3 - X4.stl
127.0 x 43.2 x 40.8

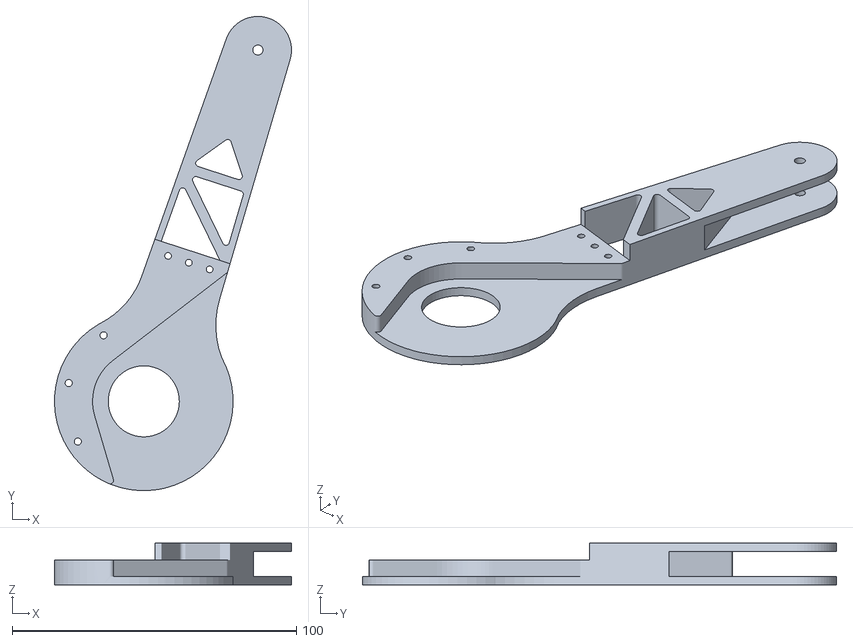
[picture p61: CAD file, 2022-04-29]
PolyDog_v2/3D-PRINTED-PART/Left_side_pieces/femur v2 gauche - x2.stl
83.4 x 166.8 x 14.8

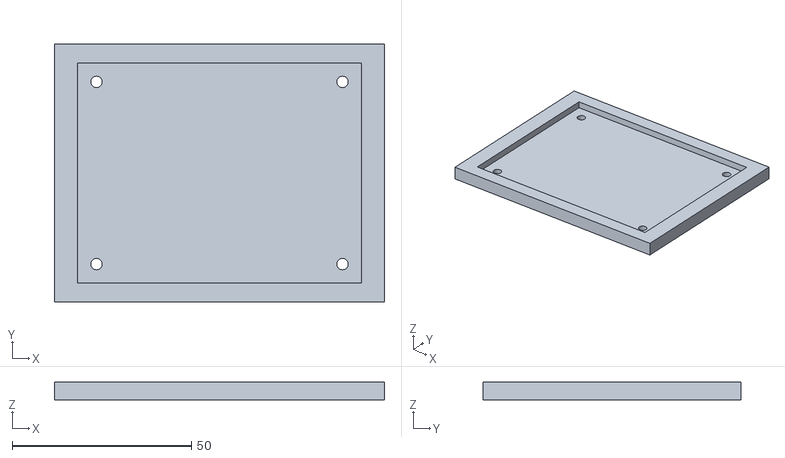
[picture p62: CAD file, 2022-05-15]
PolyDog_v2/3D-PRINTED-PART/support SSC32.stl
92.0 x 72.0 x 5.00

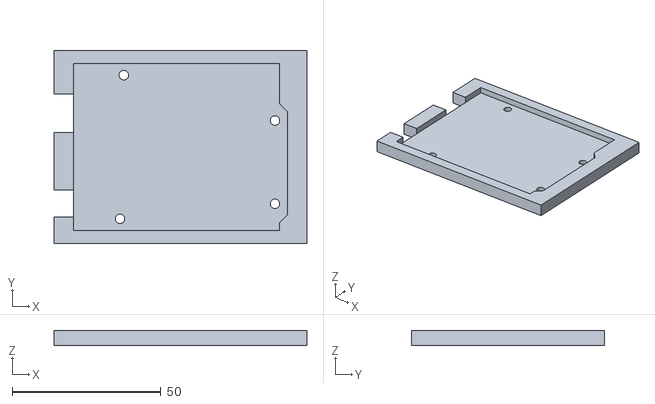
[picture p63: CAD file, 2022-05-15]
PolyDog_v2/3D-PRINTED-PART/support arduinoUNO.stl
85.0 x 65.0 x 5.00

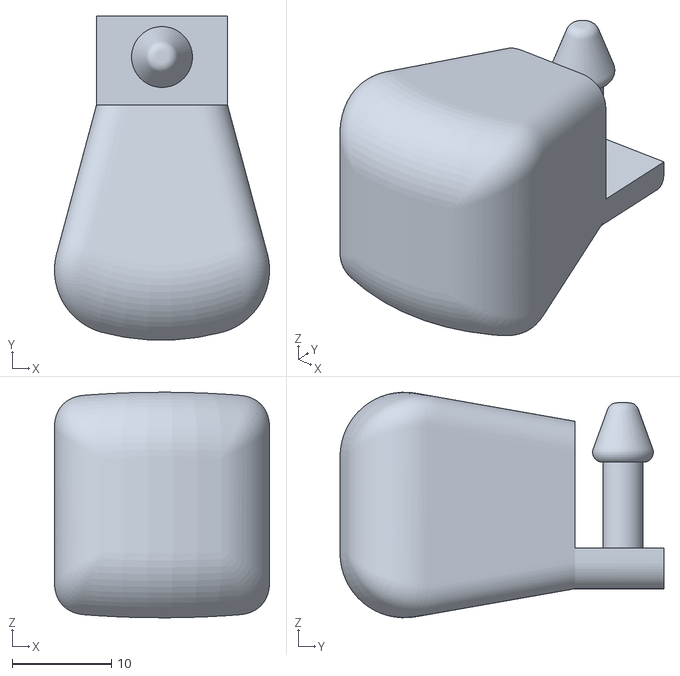
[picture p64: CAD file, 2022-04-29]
PolyDog_v2/3D-PRINTED-PART/pied_v2-X4.stl
21.7 x 32.7 x 22.7

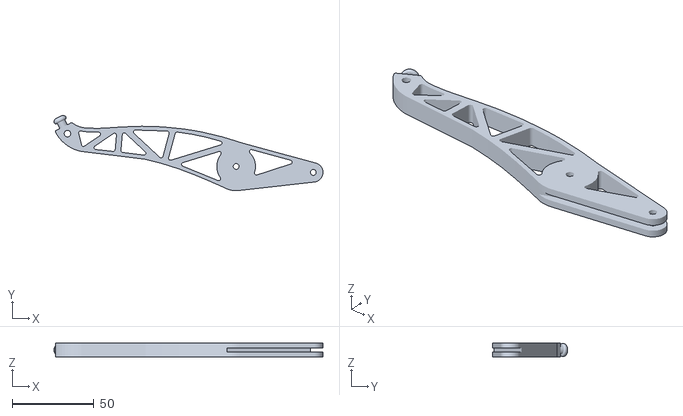
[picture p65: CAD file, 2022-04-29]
PolyDog_v2/3D-PRINTED-PART/tibia-x4.stl
164.2 x 46.0 x 8.63

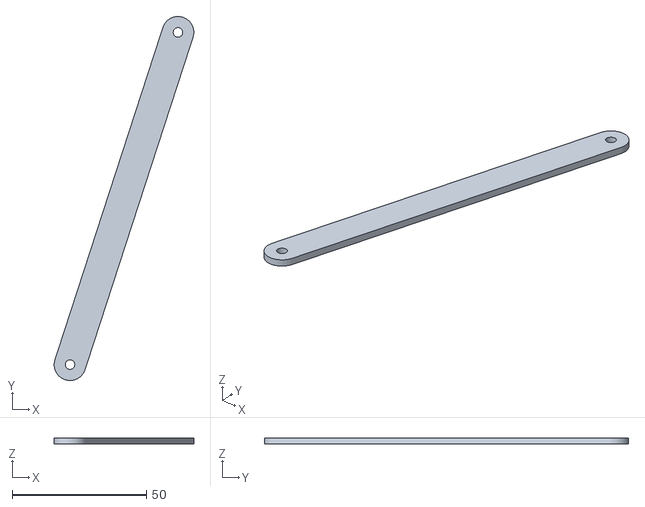
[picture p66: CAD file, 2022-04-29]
PolyDog_v2/3D-PRINTED-PART/tendon-x4.stl
52.0 x 135.4 x 2.36

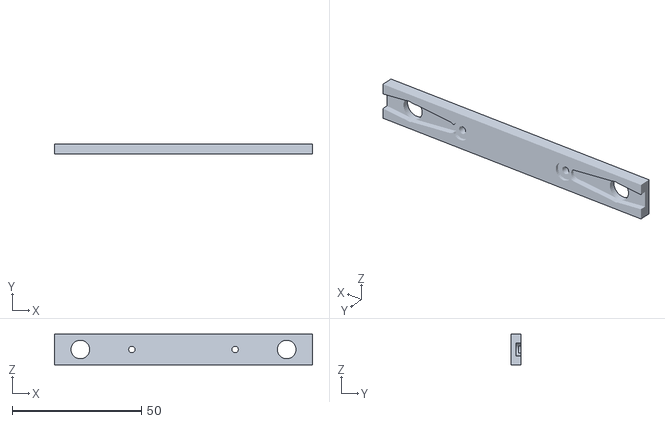
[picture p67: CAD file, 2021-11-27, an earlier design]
PolyDog_v1/docs/research/KITtyBot/kittybot_3D_bumper.stl
100.0 x 4.00 x 12.0

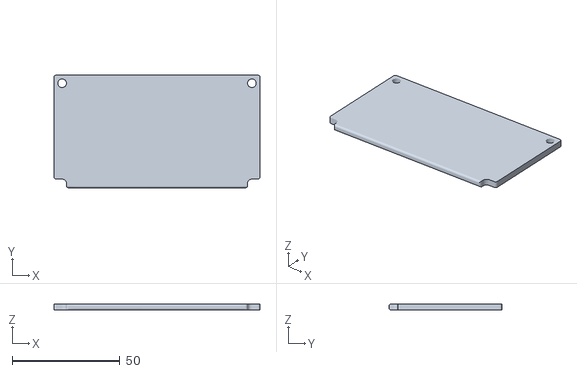
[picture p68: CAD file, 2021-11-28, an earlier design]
PolyDog_v1/docs/research/PADWQ_open_source-main/STL/Padwq_bat_side (1).stl
95.6 x 52.4 x 3.00

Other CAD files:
PolyDog_v2/3D-PRINTED-PART/Left_side_pieces/genou v2 gauche - xx2.stl
PolyDog_v2/3D-PRINTED-PART/Right_side_pieces/hanche cran v2 droit- xx2.stl
PolyDog_v2/3D-PRINTED-PART/Right_side_pieces/femur v2 droit - x2.stl
PolyDog_v1/docs/research/quadruped_robot_diy/STL_Files/ESP32_Bracket_Mirror.stl
PolyDog_v1/docs/research/KITtyBot/kittybot_3D_body.stl
PolyDog_v1/docs/research/KITtyBot/kittybot_3D_final.stl
PolyDog_v1/docs/research/KITtyBot/kittybot_3D_lower_leg.stl
PolyDog_v1/docs/research/KITtyBot/kittybot_3D_servo_support.stl
PolyDog_v1/docs/research/KITtyBot/kittybot_3D_thigh.stl
PolyDog_v1/docs/research/PADWQ_open_source-main/STL/Body584.stl
PolyDog_v1/docs/research/PADWQ_open_source-main/STL/Body63_1.stl
PolyDog_v1/docs/research/PADWQ_open_source-main/STL/M1_limit.stl
PolyDog_v1/docs/research/PADWQ_open_source-main/STL/MH12 v8.stl
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

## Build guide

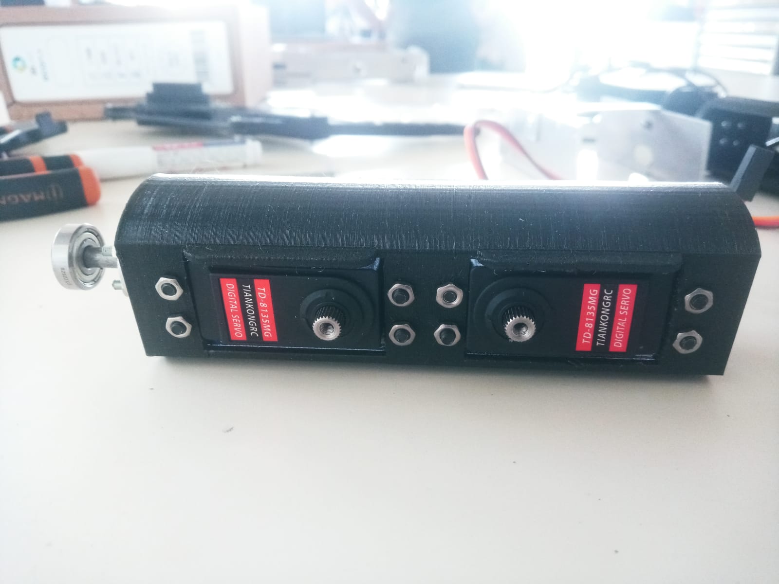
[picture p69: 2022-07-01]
PolyDog_v2/rapports_seances_hugo_durand/seance04_hugo_durand/installation_moteur_vuedevant.jpeg

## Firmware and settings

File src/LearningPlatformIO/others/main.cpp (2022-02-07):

// #include <CustomServos.h>
// #include <Arduino.h>
// #include <Servo.h>

// CustomServos servo01(2, 0, 180);
// CustomServos servo02(3, 0, 180);
// CustomServos servo03(4, 0, 180);
// CustomServos servo04(5, 0, 180);
// CustomServos servo05(6, 0, 180);
// CustomServos servo06(7, 0, 180);
// CustomServos servo07(8, 0, 180);
// CustomServos servo08(9, 0, 180);
// CustomServos servo09(10, 0, 180);
// CustomServos servo10(11, 0, 180);
// CustomServos servo11(12, 0, 180);
// CustomServos servo12(13, 0, 180);

// float A;
// float B;
// float C;
// float a = 9.7;
// float b;
// float c = 10;

// int angle_genou;
// int angle_hanche;

// int Bint;
// int Cint;

// float fmap(float x, float a, float b, float c, float d)
// {
//     float f = x / (b - a) * (d - c) + c;
//     return f;
// }

// void setup()
// {
//     // servo01.attach();
//     // servo02.attach();
//     // servo03.attach();
//     // servo04.attach();
//     // servo05.attach();
//     // servo06.attach();
//     // servo07.attach();
//     // servo08.attach();
//     // servo09.attach();
//     servo10.attach();
//     servo11.attach();
//     servo12.attach();

//     Serial.begin(9600);
// }

// void loop()
// {
//     // Calculated for C leg
//     b = fmap((float)analogRead(1), 0.0, 1023.0, 10.5, 19.3);

//     B = acos(b / (2 * a)) * 180 / PI;
//     C = 180 - (180 - 2 * B);

//     Cint = (int)C;
//     Bint = (int)B;

//     angle_genou = (90 - Cint);
//     angle_hanche = (90 - Bint) * 40 / 25;
//     // End of calculated for C leg

//     Serial.print("hanche: ");
//     Serial.print(angle_hanche);
//     Serial.print("     genou: ");
//     Serial.print(angle_genou);
//     Serial.print("     height: ");
//     Serial.println(b);

//     servo03.write(angle_genou);                       //genou A
//     servo02.write(angle_hanche);                      //hanche A
//     servo01.write(41);                                //epaule A -> value to be at 90 from ground
//     servo06.write(76);                                //epaule B -> value to be at 90 from ground
//     servo05.write(map(angle_hanche, 0, 180, 180, 0)); //hanche B
//     servo04.write(angle_genou);                       //genou B
//     servo09.write(angle_genou);                       //genou C
//     servo08.write(map(angle_hanche, 0, 180, 180, 0)); //hanche C
//     servo07.write(158);                               //epaule C -> value to be at 90 from ground
//     servo12.write(92);                                //epaule D -> value to be at 90 from ground
//     servo11.write(angle_hanche);                      //hanche D
//     servo10.write(angle_genou);                       //genou D
// }

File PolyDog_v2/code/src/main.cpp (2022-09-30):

// Copyright (c) 2022-2022. ANJOU Raphaël & DURAND Hugo
//
// Licensed under the Apache License, Version 2.0 (the "License");
// you may not use this file except in compliance with the License.
// You may obtain a copy of the License at
//
// http://www.apache.org/licenses/LICENSE-2.0
//
// Unless required by applicable law or agreed to in writing, software
// distributed under the License is distributed on an "AS IS" BASIS,
// WITHOUT WARRANTIES OR CONDITIONS OF ANY KIND, either express or implied.
// See the License for the specific language governing permissions and
// limitations under the License.

#include <Arduino.h>
#include "PolyDog/PolyDog.h"
#include "CustomServo/CustomServo.h"
#include "Leg/Leg.h"
#include <IRremote.h>
#include <Pixy2.h>
#include <PIDLoop.h>

// ------ INITIALIZATION ------
Pixy2 pixy;
PIDLoop panLoop(400, 0, 400, true);
PIDLoop tiltLoop(500, 0, 500, true);

PolyDog dog = PolyDog();

int IrReceiverPin = 8;
decode_results results;
IRrecv IRreceiver(IrReceiverPin);

int remote_choice = 0; // Default choice : robot is standing and not moving
// ------ END OF INITIALIZATION ------

/**
 * This method translates the button pushed on the remote to a number that can then be used to know which method
 * needs to be execute in the main loop. Assigning the choice to a variable makes it possible to push a button only once
 * and still have the method running in the main loop.
 *
 * @param results the data received by the infrared receiver
 * @return a number between 0 and 16 which is later used to decide which method needs to be called
 */
int getRemoteChoice(uint32_t results)
{
    switch (results)
    {

    case 0xFF629D: // button UP
        remote_choice = 12;
        break;
    case 0xFFC23D: // button RIGHT
        remote_choice = 13;
        break;
    case 0xFFA857: // button BOTTOM
        remote_choice = 14;
        break;
    case 0xFF22DD: // button LEFT
        remote_choice = 15;
        break;
    case 0xFF02FD: // button CENTER
        remote_choice = 16;
        break;
    case 0xFF6897: // button 1
        remote_choice = 1;
        break;
    case 0xFF9867: // button 2
        remote_choice = 2;
        break;
    case 0xFFB04F: // button 3
        remote_choice = 3;
        break;
    case 0xFF30CF: // button 4
        remote_choice = 4;
        break;
    case 0xFF18E7: // button 5
        remote_choice = 5;
        break;
    case 0xFF7A85: // button 6
        remote_choice = 6;
        break;
    case 0xFF10EF: // button 7
        remote_choice = 7;
        break;
    case 0xFF38C7: // button 8
        remote_choice = 8;
        break;
    case 0xFF5AA5: // button 9
        remote_choice = 9;
        break;
    case 0xFF42BD: // button *
        remote_choice = 10;
        break;
    case 0xFF4AB5: // button 0
        remote_choice = 0;
        break;
    case 0xFF52AD: // button #
        remote_choice = 11;
        break;
    }

    return remote_choice;
}

/**
 * This method is executed only once at the beginning of the program.
 * It initialize the Serial communication (baud rate = 115200), the PolyDog instance, the infrared communication and the
 * Pixy Cam.
 */
void setup()
{
    dog.start();
    Serial.begin(115200);
    IRreceiver.enableIRIn();

    pixy.init();
    pixy.changeProg("color_connected_components");
}

/**
 * This method is a loop that is executed infinitely right after the setup(). It manages the logic of which method is
 * executed by the robot. It also reads the value from the infrared remote.
 */
void loop()
{
    // dog.start();
    dog.move_forward();
    // dog.control_with_potentio();

    /**
    if (IRreceiver.decode())
    {
        IRreceiver.resume();
        remote_choice = getRemoteChoice(IrReceiver.decodedIRData.decodedRawData);
    }

    delay(100);

    switch (remote_choice)
    {
    case 0: // button 0
            // Camera mode : the dog is following an object

        int32_t panOffset, tiltOffset;

        // get active blocks from Pixy
        pixy.ccc.getBlocks();

        if (pixy.ccc.numBlocks)
        {

            // calculate pan and tilt "errors" with respect to first object (blocks[0]),
            // which is the biggest object (they are sorted by size).
            panOffset = (int32_t)pixy.frameWidth / 2 - (int32_t)pixy.ccc.blocks[0].m_x;
            tiltOffset = (int32_t)pixy.ccc.blocks[0].m_y - (int32_t)pixy.frameHeight / 2;

            // update loops
            panLoop.update(panOffset);
            tiltLoop.update(tiltOffset);

            // set pan and tilt servos
            pixy.setServos(panLoop.m_command, tiltLoop.m_command);

            dog.move_forward();
        }
        else // no object detected, go into reset state
        {
            panLoop.reset();
            tiltLoop.reset();
            pixy.setServos(panLoop.m_command, tiltLoop.m_command);
        }

        break;
    case 1:
    case 2:
    case 3:
    case 4:
    case 5:
    case 6:
    case 7:
    case 8:
    case 9:
        break;
    case 10: // * button
        // The robot is in a waiting movement, juste like a game player waiting
        dog.self_balancing();
        break;
    case 11: // # button
        // The robot is doing a little excitement thing
        dog.excitement();
        break;
    case 12: // UP button
        // The robot is going forward
        dog.move_forward();
        break;
    case 13: // RIGHT button
        // The robot is going to the right
        dog.move_right();
        break;
    case 14: // DOWN button
        // The robot is going backward
        break;
    case 15: // LEFT button
        // The robot is going to the left
        dog.move_left();
        break;
    case 16: // OK button
        // ROBOT IS STATIC
        dog.start();
        break;
    default:
        break;
    }**/
}

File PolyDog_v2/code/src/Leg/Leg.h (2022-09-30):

// Copyright (c) 2022-2022. ANJOU Raphaël & DURAND Hugo
//
// Licensed under the Apache License, Version 2.0 (the "License");
// you may not use this file except in compliance with the License.
// You may obtain a copy of the License at
//
// http://www.apache.org/licenses/LICENSE-2.0
//
// Unless required by applicable law or agreed to in writing, software
// distributed under the License is distributed on an "AS IS" BASIS,
// WITHOUT WARRANTIES OR CONDITIONS OF ANY KIND, either express or implied.
// See the License for the specific language governing permissions and
// limitations under the License.

/**
 * @file Leg.h
 *
 * @brief Leg object used to control one leg of the robot
 *
 * @author ANJOU Raphael
 * <p>
 * Contact: anjou.raphael\@gmail.com
 *
 */

#ifndef LEG_H
#define LEG_H

#include <Arduino.h>
#include "CustomServo/CustomServo.h"

/**
 * A {@code Leg} object allows you to control one of the robot leg.
 *
 * The leg that is controlled can be chosen when initializing with the parameter {@code leg_number}
 *
 * There are many constants and they are all specific to a certain leg.
 * Some are used to calculate correctly the angle to go to for the servos.
 * Some are used to assign which servos are used by the leg.
 *
 * @author ANJOU Raphael
 */
class Leg
{
public:
    /**
     * This method is the {@code Leg} initializer
     * @param leg_number The leg chosen, this value will affects which servos and constants are used
     */
    Leg(int leg_number);
    Leg();
    /**
     * This method will move the knee servo to the correct angle by considering the offsets constants
     * @param angle The desired angle to move the servo to
     */
    void move_knee(int angle, int offset);

    void move_knee(int angle);

    /**
     * This method will move the hip servo to the correct angle by considering the offsets constants
     * @param angle The desired angle to move the servo to
     */
    void move_hip(int angle, int offset);

    // TO REMOVE
    void move_hip(int angle);

    /**
     * This method will move the shoulder servo to the correct angle by considering the min and max constants
     * @param angle The desired angle to move the servo to
     */
    void move_shoulder(int angle);

    // Constants for LEG A
    int OFFSET_KNEE_A = 0;
    int OFFSET_HIP_A = 0;
    int ANGLE_MIN_SHOULDER_A = 185; // 160
    int ANGLE_MAX_SHOULDER_A = 5;   // -15
    CustomServo SERVO_SHOULDER_A = CustomServo(13);
    CustomServo SERVO_HIP_A = CustomServo(14);
    CustomServo SERVO_KNEE_A = CustomServo(15);

    // Constants for LEG B
    int OFFSET_KNEE_B = -38; // -18 -> 100 : -28 -> 90 : -28 -> 100 : -38
    int OFFSET_HIP_B = 40;   // 60 -> 141 : 0 -> 81 : 9 -> 90 : 9 -> 59
    int ANGLE_MIN_SHOULDER_B = -5;
    int ANGLE_MAX_SHOULDER_B = 180;
    CustomServo SERVO_SHOULDER_B = CustomServo(2);
    CustomServo SERVO_HIP_B = CustomServo(1);
    CustomServo SERVO_KNEE_B = CustomServo(0);

    // Constants for LEG C
    int OFFSET_KNEE_C = 179;
    int OFFSET_HIP_C = 240;
    int ANGLE_MIN_SHOULDER_C = 185;
    int ANGLE_MAX_SHOULDER_C = 5;
    CustomServo SERVO_SHOULDER_C = CustomServo(18);
    CustomServo SERVO_HIP_C = CustomServo(17);
    CustomServo SERVO_KNEE_C = CustomServo(16);

    // Constants for LEG D
    int OFFSET_KNEE_D = 176;
    int OFFSET_HIP_D = 190;
    int ANGLE_MIN_SHOULDER_D = -15;
    int ANGLE_MAX_SHOULDER_D = 165;
    CustomServo SERVO_SHOULDER_D = CustomServo(26);
    CustomServo SERVO_HIP_D = CustomServo(27);
    CustomServo SERVO_KNEE_D = CustomServo(25);

private:
    int _leg_number;
    int _knee_offset;
    int _hip_offset;
    int _ANGLE_MIN_SHOULDER;
    int _ANGLE_MAX_SHOULDER;
    CustomServo _knee_servo;
    CustomServo _hip_servo;
    CustomServo _shoulder_servo;
};
#endif

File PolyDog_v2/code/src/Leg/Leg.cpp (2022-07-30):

// Copyright (c) 2022-2022. ANJOU Raphaël & DURAND Hugo
//
// Licensed under the Apache License, Version 2.0 (the "License");
// you may not use this file except in compliance with the License.
// You may obtain a copy of the License at
//
// http://www.apache.org/licenses/LICENSE-2.0
//
// Unless required by applicable law or agreed to in writing, software
// distributed under the License is distributed on an "AS IS" BASIS,
// WITHOUT WARRANTIES OR CONDITIONS OF ANY KIND, either express or implied.
// See the License for the specific language governing permissions and
// limitations under the License.

#include <Arduino.h>
#include "CustomServo/CustomServo.h"
#include "Leg/Leg.h"

/**
 * This method will initialize a {@code Leg} object.
 * It uses {@code leg_number} to know which motors and constants need to be assigned to the object.
 *
 * @param leg_number this number will tell which leg of the robot needs to be used. This will affect minimum and maximum
 * values as well as offset
 * @author ANJOU Raphael
 */
Leg::Leg(int leg_number)
{
    _leg_number = leg_number;

    switch (_leg_number)
    {
    case 1:
        _knee_servo = SERVO_KNEE_A;
        _hip_servo = SERVO_HIP_A;
        _shoulder_servo = SERVO_SHOULDER_A;
        _knee_offset = OFFSET_KNEE_A;
        _hip_offset = OFFSET_HIP_A;
        _ANGLE_MIN_SHOULDER = ANGLE_MIN_SHOULDER_A;
        _ANGLE_MAX_SHOULDER = ANGLE_MAX_SHOULDER_A;
        break;

    case 2:
        _knee_servo = SERVO_KNEE_B;
        _hip_servo = SERVO_HIP_B;
        _shoulder_servo = SERVO_SHOULDER_B;
        _knee_offset = OFFSET_KNEE_B;
        _hip_offset = OFFSET_HIP_B;
        _ANGLE_MIN_SHOULDER = ANGLE_MIN_SHOULDER_B;
        _ANGLE_MAX_SHOULDER = ANGLE_MAX_SHOULDER_B;
        break;

    case 3:
        _knee_servo = SERVO_KNEE_C;
        _hip_servo = SERVO_HIP_C;
        _shoulder_servo = SERVO_SHOULDER_C;
        _knee_offset = OFFSET_KNEE_C;
        _hip_offset = OFFSET_HIP_C;
        _ANGLE_MIN_SHOULDER = ANGLE_MIN_SHOULDER_C;
        _ANGLE_MAX_SHOULDER = ANGLE_MAX_SHOULDER_C;
        break;

    case 4:
        _knee_servo = SERVO_KNEE_D;
        _hip_servo = SERVO_HIP_D;
        _shoulder_servo = SERVO_SHOULDER_D;
        _knee_offset = OFFSET_KNEE_D;
        _hip_offset = OFFSET_HIP_D;
        _ANGLE_MIN_SHOULDER = ANGLE_MIN_SHOULDER_D;
        _ANGLE_MAX_SHOULDER = ANGLE_MAX_SHOULDER_D;
        break;

    default:
        break;
    }
}

/**
 * This method will move the knee to the desired angle.
 *
 * The class value _knee_offset allows us to give the same angle to all motors.
 * If it was not there, motors that are upside down would be going in the opposite direction of the others.
 *
 * @param angle the angle wanted for the servo
 * @author ANJOU Raphael
 */
void Leg::move_knee(int angle, int offset)
{
    // _knee_servo.write(abs(_knee_offset - angle));
    _knee_servo.write(abs(offset - angle));
}

void Leg::move_knee(int angle)
{
    _knee_servo.write(abs(_knee_offset - angle));
}

/**
 * This method will move the hip to the desired angle.
 *
 * The class value _hip_offset allows us to give the same angle to all motors.
 * If it was not there, motors that are upside down would be going in the opposite direction of the others.
 *
 * @param angle the angle wanted for the servo
 * @author ANJOU Raphael
 */
void Leg::move_hip(int angle, int offset)
{
    // _hip_servo.write(abs(_hip_offset - angle));
    _hip_servo.write(abs(offset - angle));
}

void Leg::move_hip(int angle)
{
    _hip_servo.write(abs(_hip_offset - angle));
}

/**
 * This method will move the shoulder to the desired angle.
 *
 * _ANGLE_MIN_SHOULDER and _ANGLE_MAX_SHOULDER are values that needs to be manually written.
 * The first one corresponds to the angle where the leg is parallel to the ground and facing upward.
 * The second one corresponds to the angle where the leg is parallel to the ground and facing downward.
 * Therefore, thanks to this calibration, 90° will always be the value where the leg is perpendicular to the ground.
 *
 * @param angle the angle wanted for the servo
 * @author ANJOU Raphael
 */
void Leg::move_shoulder(int angle)
{
    _shoulder_servo.write(map(angle, 0, 180, _ANGLE_MIN_SHOULDER, _ANGLE_MAX_SHOULDER));
}

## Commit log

2021-11-24 Added M. Masson documents about the Arduino project course
2021-11-24 Created test folder and test_list.md. I've continued writing the cahier des charges.
2021-11-27 Did a lot of research about existing similar project and about inverse dynamic
    [kittybot_3D_body.stl, kittybot_3D_bumper.stl, kittybot_3D_final.stl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]
2021-11-27 Addition of the stages of the realization of our project
2021-11-27 Created new research directory to differentiate from docs directory
    [kittybot_3D_body.stl, kittybot_3D_bumper.stl, kittybot_3D_final.stl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]
2021-11-27 Added diy quadruped robot example
    [6.ESP-32_Predeterminado.ipt, 6800 Ball.ipt, 6800 Inner Ring.ipt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]
2021-11-27 Added lfs management for quadruped_robot_example folder
    [6.ESP-32_Predeterminado.ipt, 6800 Ball.ipt, 6800 Inner Ring.ipt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]
2021-11-28 Added tons of robot example and stl files
    [Body584.stl, Body63_1.stl, M1_limit.stl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]
2021-11-28 Renamed a hugo's directory containing the 3D shape a miniature prototype. Created a new one to store the final 3D files for our robot. Completed my seance00_raphael_anjou.md with what we had done unt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
2021-11-28 Ajout des parties de la jambe à imprimer
    [MH12 v8.stl, Padwq_MH23.stl, Padwq_MH32.stl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]
2021-11-30 Started my first session report and done a leg part miniature folder ready for 3D printer
    [ball_h.stl, ball_leg4_1.stl, leg1-1.stl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]
2021-12-02 Added some 3d parts
    [Channel Bracket.SLDPRT, Offset Bracket.SLDPRT, U Bracket.SLDPRT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]
2021-12-03 completed seance01_raphael_anjou.md
    [leg1.stl, leg5.stl]
2021-12-17 Achevé mon rapport de séance 2
    [Channel Bracket.SLDPRT, MH12 v8.stl, Offset Bracket.SLDPRT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]
2022-01-07 Ecrit rapport de seance ajouté dossier impression
    [boitier - boitier.stl, engrenage 1 accessoire - engrenage01 (25 teeth).stl, femur - femur.stl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]
2022-01-29 Moved part folders. Created platform io project structure. Created first example lib.
    [Channel Bracket.SLDPRT, MH12 v8.stl, Offset Bracket.SLDPRT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]
2022-01-29 Morse library is an example from Arduino Docs Created basic library for servos. Still can't really understand Platform IO. Port not detected.
2022-01-31 Added old ino files. Changed main to activate all 12 motors.
2022-01-31 Spent all evening trying to have the robot stand up with specified value for the servos. Managed to do it.
2022-02-02 Worked on inverse kinematics. Trying to make the feet move up and down lineary
2022-02-03 Added information about servos placement.
2022-02-03 Found process to install legs properly. Shoulders still not correct, specific angles chosen.
    [main.cpp]
2022-02-05 Rédiger le rapport de séance 5
2022-02-06 Réintégration de main.cpp
2022-02-07 Leg routine to go forward. Robot walked for the first time ever :) Worked on creating new class PolyDog. Completed class CustomServos
2022-02-08 FINALLY WORKING ! The class PolyDog can now be used and motors are well driven.
2022-02-08 Cleaned the project directory. Cleaned code in src. Added new project PlatformIO : PolyDogPIO to be used as our correct directory.
    [main.cpp, run_servo.cpp]
2022-02-10 Rapport de séance
2022-02-15 Still trying to work out the leg movement while making improvement in the classes.
2022-02-17 Adaptation code for ssc-32 servo controller
2022-02-17 Remove bugs on Plateformio / The code works again on the ssc-32 servo controller
    [PolyDog.cpp, main.cpp]
2022-02-17 Fixed the robot. Was a bug in the setup of the hardware (ssc32 baud rate to configure directly with the hardware)
    [PolyDog.cpp, main.cpp]
2022-02-24 Continuation du code de la marche
2022-02-25 Try to commit even though i know there are some problems
    [Leg.cpp, Leg.h, PolyDog.cpp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]
2022-02-25 Added Leg class. Allows to control each servo from a single leg with their correct offsets. Leg parameter allows you to chose which leg will be controled.
    [Leg.cpp, Leg.h, PolyDog.cpp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]
2022-02-25 Leg class is working. Offset are all calculated correctly. Min and max value for shoulder correct.
    [Leg.cpp, Leg.h, PolyDog.cpp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]
2022-02-26 saving my work before trying to add the camera
2022-02-26 Corrections and added move_left()
    [PolyDog.cpp, main.cpp]
2022-03-08 Mise à jour #Readme et rapport de séance
2022-03-10 Ajout d'images pour la présentation d'Arduino
2022-03-11 Added 3D pieces used with STL files
    [Plateau de base_v3 - Engines support plate.stl, boitier_v2 - Left Part.stl, boitier_v2 - Right Part.stl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]
2022-03-15 Update Cahier des charges
2022-03-15 Project Polydog_V1
    [6.ESP-32_Predeterminado.ipt, 6800 Ball.ipt, 6800 Inner Ring.ipt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]
2022-04-29 Commit nouveaux avancements
    [femur droit v2 - x2.stl, femur v2 gauche - x2.stl, genou v2 - droit x2.stl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]
2022-04-30 Changed underscores to dash in nearly all project
    [6.ESP-32_Predeterminado.ipt, 6800 Ball.ipt, 6800 Inner Ring.ipt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]
2022-04-30 Move polydog-v2 3d parts
    [femur droit v2 - x2.stl, femur v2 gauche - x2.stl, genou v2 - droit x2.stl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]
2022-04-30 Clean the robot-parts folder. Add every correct part.
    [Channel Bracket.SLDPRT, MH12 v8.stl, Offset Bracket.SLDPRT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]
2022-04-30 Add STL and OnShape files of every 3d-parts of the V1
    [back.stl, back.x_t, base.stl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]
2022-05-01 Rename the preview of the servo bracket
2022-05-01 docs: Add table of leg parts and body parts to the README
2022-05-01 docs: Still working on the README. Clean up of the directory.
    [6.ESP-32_Predeterminado.ipt, 6800 Ball.ipt, 6800 Inner Ring.ipt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]
2022-05-14 fixed merge conflict and clean repo
    [femur droit v2 - x2.stl, femur v2 gauche - x2.stl, genou v2 - droit x2.stl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]
2022-05-14 chore: rename polydog-v1 to PolyDog_V1
    [6.ESP-32_Predeterminado.ipt, 6800 Ball.ipt, 6800 Inner Ring.ipt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]
2022-05-15 Update pieces and add support for ssc32 and uno
    [boitier v3 - X4.stl, genou v2 droit - x2.stl, genou v2 droit- xx2.stl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]
2022-06-25 changes 3D printed part
    [hanche cran v2 gauche - xx2.stl, hanche cran v2 gauche --.stl, v2-engrenage 1 accessoire - ESSAI2.stl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]
2022-07-30 feat: all legs should be correctly parameterized
    [Leg.cpp, Leg.h, PolyDog.cpp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]
